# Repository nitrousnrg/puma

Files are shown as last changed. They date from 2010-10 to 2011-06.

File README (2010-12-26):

This is the hardware design of FreeEMS, a free engine management system.

Originally developed by jharvey, this branch uses his schematics, but adds a few extra circuits and redesigns the pcb, in order to fit the argentinian market better.

This design is NOT INTENDED to be as configurable as the official hardware, but to be suitable for production.

Main goals are:
* SMD
* 2 layers, 10x13cm board
* connector board for engine interface
* industrial grade specs
* 8 hi/low Z injector outputs
* 4 ignition outputs
* fuel pump control
* stepper motor control
* 2 aux power outputs
* MAP, AAP, MAF, TPS, lambda, battery voltage, EGT, MAT, IAT, CLT, aux temperature input, aux GP input
* 6 protected GPIO
* USB for tuning and datalogging

Planned release: 20/6/2011 (or never)

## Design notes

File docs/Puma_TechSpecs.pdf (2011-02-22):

Puma is an automotive-grade board designed to run FreeEMS vanilla code, an Open Source Engine Management System destined to liberate engines all around the globe. This piece of hardware was meant to meet the highest reliability standards, and to provide most of the functions needed by engine tuners. It has the potential to sequentially drive up to 8 cylinder engines, controlling both fuel and ignition (wasted spark), or dual rail 4 cylinders setups, 6cyl, etc. With the appropiate firmware, almost anything can be done.

These boards come with military temperature specs, and plenty of heavy duty components.

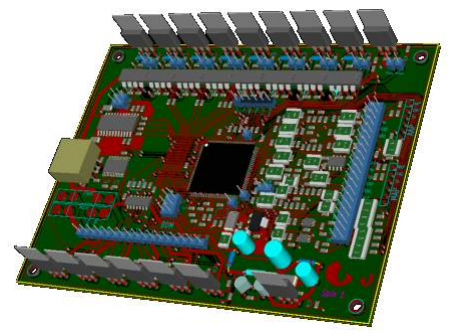
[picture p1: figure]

### Capabilities

Every board is equipped with the following items:

- USB connection for engine tuning, datalogging, and firmware updates.
- Compact SMD assembly.
- 8 outputs for low impedance injectors.
- 4 ignition outputs.
- 2 general purpose power outputs.
- 12 analog inputs
- 12 digital general purpose I/O
- Stepper driver
- Fuel pump relay control
- CAN and SPI communications
- Connector board to suit different setups, allow extra features, and provide different connectors or prototyping areas.

### Inputs

- MAP (Manifold Absolute Pressure)
- MAF (Mass Air Flow sensor)
- CHT (Coolant temperature)
- AAP (Atmospheric Absolute Pressure)
- IAT (Intake Air Temperature)
- EGO (Exhaust Gas Oxygen)
- BVR (Battery Voltage Reference)
- MAT (Manifold Air Temperature)
- EGT (Exhaust Gas Temperature)
- Aux NTC sensor
- General purpose analog input
- 2 VR inputs

### Outputs

- 8 Peak & Hold injector drivers supplying up to 4 Amps each.
- 4 ignition outputs, intended to drive external ignition modules, although ignition drivers can be installed.
- 2 PWM outputs, capable of delivering many amps to solenoid valves, switches, servos, etc.
- 1 output for controlling the fuel pump relay

Extra CPU pins can be used through specific connector boards (not designed yet!), for example

- 2 extra ignition outputs can be used for 6 cylinders COP setups
- Up to 10 general purpose power outputs (pumps, nitrous triggers, extra solenoids, etc)

### Specs

- Input voltage: 6.5v-32v (to be tested)
- Operating temperature: -40°C to 125°C (its the target, still not reached)
- Reverse battery protection
- All inputs protected from overvoltages.
- Power outputs clamped to 33v (can change soon)

### Connector board

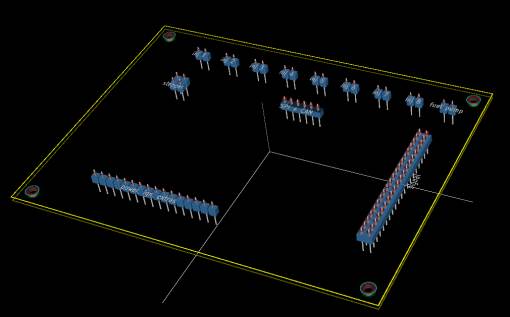
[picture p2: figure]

The first draft is still subject to change, until we find a better way to connect the high power parts.

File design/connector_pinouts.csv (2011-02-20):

connector pin outs (for spin 1 of puma)
P99
pin | MCU/destination | nick name | DIGI PROTECT | AN PROTECT | PG (1 AND …) | bried descrition
1 |  | MAT |  |  | 26 | MAS AIR TEMP THERMISTOR INPUT PG 26
2 |  | AGND |  |  | 26
3 |  | AUX IN |  |  | 10
4 |  | GP_NTC |  |  | 10 23 25 | THERMISTOR INPUT PG25
5 |  | AGND |  |  | 25 | THERMISTOR INPUT PG25
6 |  | 5 |  |  | 44
7 |  | MAP |  |  | 44 | NOT AAP
8 |  | AGND? |  |  | 44
9 |  | O2+ |  | Y | 49 | O2+
10 |  | O2GND |  |  | 49 | O2 AGND
11 |  |  |  |  |  | NC
12 |  |  |  |  |  | NC
13 |  |  |  |  |  | NC
14 |  |  |  |  |  | NC
15 |  | MAF |  |  | 23
16 | PM2 | DGP |  |  | 1 | Digital General Purpose include digi_protect sub circuit
17 |  | K+ |  |  | 21 | EGT +
18 | PM3 | DGP |  |  | 1 | Digital General Purpose include digi_protect sub circuit
19 |  | K- |  |  | 21 | EGT -
20 |  | 5 |  |  | 54 | TPS +5
21 |  | TPS |  |  | 54 | THROTTLE POSITION SENSOR
22 |  | AGND |  |  | 54 | TPS AGND
23 |  | CHT |  |  | 55 | THERMISTER INPUT
24 |  | AGND |  |  | 55
25 |  | IAT |  |  | 56 | INTAKE AIR TEMP THERMISTER INPUT
26 |  | AGND |  |  | 56
27 | PJ0 | DGP |  |  | 1 | Digital General Purpose include digi_protect sub circuit
28 | PJ1 | DGP |  |  | 1 | Digital General Purpose include digi_protect sub circuit
29 | PJ6 | DGP |  |  | 1 | Digital General Purpose include digi_protect sub circuit
30 | PJ7 | DGP |  |  | 1 | Digital General Purpose include digi_protect sub circuit
31 | PM0 | DGP |  |  | 1 | Digital General Purpose include digi_protect sub circuit
32 | PM1 | DGP |  |  | 1 | Digital General Purpose include digi_protect sub circuit
33 | PP6 | DGP |  |  | 1 | Digital General Purpose include digi_protect sub circuit
34 | PP7 | DGP |  |  | 1 | Digital General Purpose include digi_protect sub circuit
35 | PT6 | DGP |  |  | 1 | Digital General Purpose include digi_protect sub circuit
36 | PT7 | DGP |  |  | 1 | Digital General Purpose include digi_protect sub circuit
37 |  | VR1- |  |  | 18
38 |  | VR1+ |  |  | 18
39 |  | VR2- |  |  | 5
40 |  | VR2+ |  |  | 5
misc pins
p103 | PH0 |  |  |  | 1 | direct to MCU, not protection, placed where ever it fit/near MCU
p104 | PS3 |  |  |  | 1 | direct to MCU, not protection, placed where ever it fit/near MCU

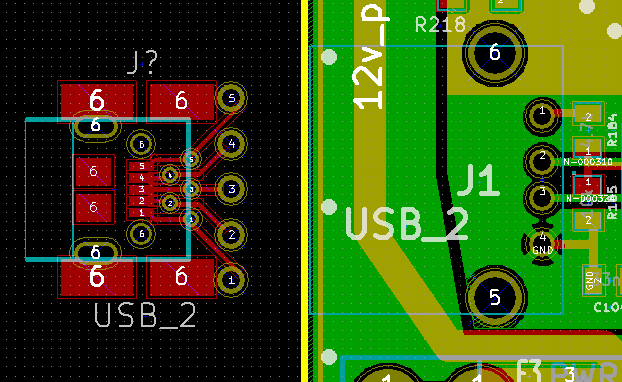
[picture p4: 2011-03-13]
PCB-modules/micro-mini-header.PNG

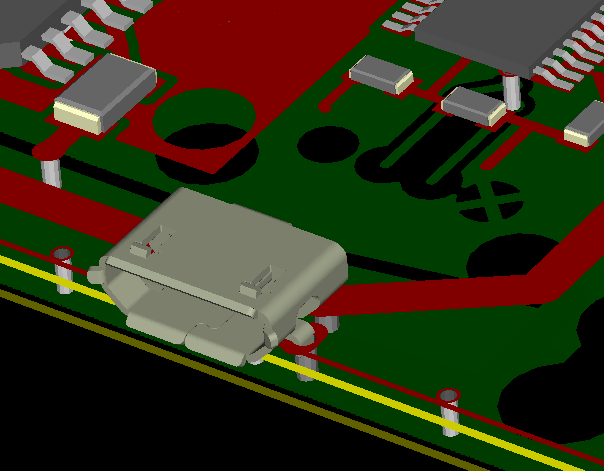
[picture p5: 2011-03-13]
PCB-modules/USB uB/USB_uB_snapshot.png

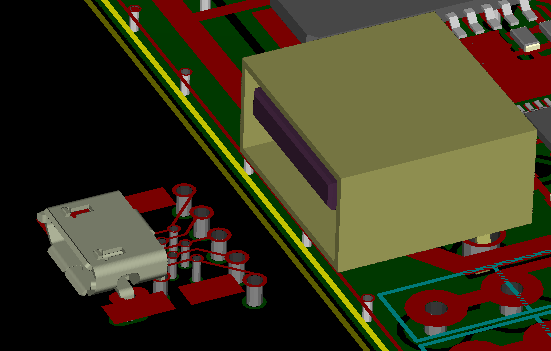
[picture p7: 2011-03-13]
PCB-modules/micro-mini-header-iso-u.PNG

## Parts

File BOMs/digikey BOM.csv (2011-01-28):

Digi-Key Part Number | Description | Mouser number | Optional? | Quantity 1 | Quantity 2
490-1664-1-ND | .01uF |  |  | 9
490-1666-2-ND | .1uF |  |  | 25
WHCR10FECT-ND | 0.1 2W |  | P&H | 8
490-1666-2-ND | 0.1uF |  |  | 15
311-1128-1-ND | 1.5nF |  |  | 11
RMCF0805JT1K00CT-ND | 1.6k |  |  | 9
RMCF0805JT100KCT-ND | 100k |  |  | 3
WK6242-ND | 10A |  |  | 1
RMCF0805JT10K0CT-ND | 10k |  |  | 25
RMCF0805JT10M0CT-ND | 10M |  |  | 1
311-1099-1-ND | 10pF |  |  | 3
493-1279-ND | 10uF |  |  | 2
644-1129-1-ND | 16MHZ |  |  | 1
RMCF0805JT1K00CT-ND | 1K |  |  | 64
1N4007DICT-ND | 1N4007 |  |  | 1
1N4148WTPMSCT-ND | 1N4148 |  |  | 14
1N4448W-FDICT-ND | 1N4448 |  |  | 1
1.0W-2-ND | 1R |  |  | 1
541-1.0VCT-ND | 1R 1W |  | Stepper driver | 2
RMCF0805JT2K20CT-ND | 2.2k |  |  | 7
565-1634-ND | 2200uF |  |  | 1
RMCF0805JT22K0CT-ND | 22k |  |  | 3
709-1172-1-ND | 22pF |  |  | 2
478-3901-1-ND | 22uF |  |  | 2
RMCF0805JT270RCT-ND | 270R |  |  | 2
620-1158-1-ND | 2916 |  | Stepper driver | 1
WK6242-ND | 2A |  | Fuse | 1
2N6045GOS-ND | 2N6044 |  | P&H | 8
RMCF0805JT3K30CT-ND | 3.3k |  |  | 16
399-1151-1-ND | 3.3nF |  |  | 1
RMCF0805JT1K00CT-ND | 3.9K |  |  | 1
311-1123-1-ND | 330pF |  |  | 1
478-3550-1-ND | 33nF |  |  | 9
1N5364BRLGOSCT-ND | 33v 5w |  | P&H | 8
RMCF0805JT39K0CT-ND | 39k |  |  | 13
RMCF0805JT4K70CT-ND | 4.7k |  |  | 2
BZT52C5V1-FDICT-ND | 5.1v |  |  | 12
BZT52C5V1-FDICT-ND | 5V1 |  |  | 6
P680KACT-ND | 680k |  |  | 3
RMCF0805JT68K0CT-ND | 68k |  |  | 1
74HC86DR2GOSCT-ND | 74LS86 |  | XOR gate for ignition | 1
AD8497ARMZ-ND | AD597 |  | EGT driver | 1
1N4148WTPMSCT-ND | DIODE |  |  | 4
768-1007-1-ND | FT232RL |  |  | 1
475-1415-1-ND | LED |  |  | 18
LM1949N-ND | LM1949 |  | P&H | 8
LM2937ET-5.0-ND | LM2937 |  |  | 1
MAX9924UAUB+-ND | MAX9924 |  |  | 2
MC9S12XDP512MAL-ND | MC9S12XDP512 |  |  | 1
LM2937IMP-5.0CT-ND | LM2937-SOT223 |  |  | 1
MPX4100A-ND | MPX4100A |  | AAP sensor | 1
MPX4250AP-ND | MPX4250A |  | MAP sensor | 1
RFP30N06LE-ND | RFP30N06 |  | monster mosfet | 6
RFP30N06LE-ND | RFP30N06LE |  | monster mosfet | 1
MBR0520LCT-ND | SCHOTTKY |  |  | 12
UE27AC54100-ND | USB_2 |  |  | 1
AE1454-ND | USB male A-male A cable |  | connector could be changed | 1

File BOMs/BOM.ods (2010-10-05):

Description | Digikey number | Mouser number | Quantity | $ | Parts
CPU | MC9S12XDP512MAL-ND | 841-MC9S12XDP512MAG | 2 | 23.52 | 47.04
6ch digital isolator | -- | 634-SI8460AA-B-IS1 | 2 | 2.86 | 5.72
P&H driver | LM1949N-ND | -- | 8 | 4.87 | 38.96
2N6044 | -- | 610-2N6044 | 8 | 1.15 | 9.2
0.1uF cap | 490-1666-2-ND |  | 3,000 | 0.007 | 21
10pF cap | 311-1099-1-ND |  | 100 | 0.02980 | 2.98
0.1ohm 2W | WHCR10FECT-ND |  | 8 | 0.93 | 7.44
1ohm |  |  |  |  | 0
270ohm | RMCF0603JT270RCT-ND |  | 100 | 0.007 | 0.7
1k | RMCF0603JT1K00CT-ND |  | 100 | 0.007 | 0.7
2.2k | RMCF0603JT2K20CT-ND |  | 100 | 0.007 | 0.7
3.3k | RMCF0603JT3K30CT-ND |  | 100 | 0.007 | 0.7
4.7k | RMCF0603JT4K70CT-ND |  | 100 | 0.007 | 0.7
5.6k | RMCF0603JT5K60CT-ND |  | 100 | 0.007 | 0.7
10k | RMCF0603JT10K0CT-ND |  | 100 | 0.007 | 0.7
13k | -- |  |  |  | 0
18k | -- |  |  |  | 0
22k | RMCF0603JT22K0CT-ND |  | 100 | 0.007 | 0.7
39k | P39KGCT-ND |  | 100 | 0.00790 | 0.79
68k | RMCF0603JT68K0CT-ND |  | 100 | 0.007 | 0.7
100k | RMCF0603JT100KCT-ND |  | 100 | 0.007 | 0.7
680k | P680KGCT-ND |  | 100 | 0.0079 | 0.79
1.6M | P1.6MGCT-ND |  | 100 | 0.0079 | 0.79
10M | RMCF0603JT10M0CT-ND |  | 100 | 0.007 | 0.7
LM1815 | LM1815M-ND | -- | 4 |  | 0
MAX9924 | MAX9924UAUB+-ND |  | 2 | 2.52 | 5.04
5v digital reg | LM2940T-5.0-ND |  | 3 | 1.77 | 5.31
5v analog reg | LM2936MX-5.0CT-ND |  | 2 | 2.38 | 4.76
ad596 | -- | -- |  |  | 0
FT232RL | 768-1007-1-ND |  | 2 | 4.5 | 9
16MHz crystal | 535-9948-1-ND |  | 2 | 1.01 | 2.02
fuse holder | WK6242-ND |  | 10 | 0.135 | 1.35
sckottky diode | MBR0520LCT-ND |  | 100 | 0.1936 | 19.36
5.1v zener | BZT52C5V1-FDICT-ND |  | 30 | 0.25500 | 7.65
0805 green LED | 160-1179-1-ND |  | 100 | 0.05800 | 5.8
1N4148 | 1N4148WTPMSCT-ND |  | 30 | 0.25500 | 7.65
 |  |  |  |  | 210.35

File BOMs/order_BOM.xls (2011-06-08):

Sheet: FreeEMS_setup
description | qty | notes | component | bare min |  | recommended |  | INJ-H |  | INJ-L |  | IGN |  | RPM |  | MAPB |  | MAPN |  | AAP |  | MAF |  | GPO |  | O2 |  | EGT |  | TCPL |  | AN |  | STP |  | ANP |  | DGP |  | Total
bare min parts | 1 | required (MCU, PLL, TPS, USB, BDM, 5V reg, ect) | description | qty/ea |  | qty/ea |  | qty/ea |  | qty/ea |  | qty/ea |  | qty/ea |  | qty/ea |  | qty/ea |  | qty/ea |  | qty/ea |  | qty/ea |  | qty/ea |  | qty/ea |  | qty/ea |  | qty/ea |  | qty/ea |  | qty/ea |  | qty/ea |  |  | NOTES
recommended | 1 | (SWVreg, XOR, stepper) | 2916 (stepper) |  | 0 | 1 | 1 |  | 0 |  | 0 |  | 0 |  | 0 |  | 0 |  | 0 |  | 0 |  | 0 |  | 0 |  | 0 |  | 0 |  | 0 |  | 0 |  | 0 |  | 0 |  | 0 | 1
 |  |  | 1K | 1 | 1 | 4 | 4 |  | 0 |  | 0 | 1 | 1 |  | 0 |  | 0 |  | 0 |  | 0 |  | 0 |  | 0 |  | 0 |  | 0 |  | 0 |  | 0 |  | 0 | 2 | 2 |  | 0 | 8
 |  | Outputs | 1R | 1 | 1 | 2 | 2 |  | 0 |  | 0 |  | 0 |  | 0 |  | 0 |  | 0 |  | 0 |  | 0 |  | 0 |  | 0 |  | 0 |  | 0 |  | 0 |  | 0 |  | 0 |  | 0 | 3
INJ-H | 1 | [max 8] Fuel highZ (8 max low and high) | 2A | 1 | 1 |  | 0 |  | 0 |  | 0 |  | 0 |  | 0 |  | 0 |  | 0 |  | 0 |  | 0 |  | 0 |  | 0 |  | 0 |  | 0 |  | 0 |  | 0 |  | 0 |  | 0 | 1
INJ-L | 1 | [max 8] Fuel lowZ (8 max low and high) | 10k | 11 | 11 |  | 0 |  | 0 |  | 0 | 1 | 1 | 3 | 6 |  | 0 |  | 0 |  | 0 | 1 | 1 |  | 0 |  | 0 |  | 0 |  | 0 |  | 0 |  | 0 |  | 0 |  | 0 | 19
IGN | 1 | [max 4] Ignition (external drivers) | 10M | 2 | 2 |  | 0 |  | 0 |  | 0 |  | 0 |  | 0 |  | 0 |  | 0 |  | 0 |  | 0 |  | 0 |  | 0 |  | 0 |  | 0 |  | 0 |  | 0 |  | 0 |  | 0 | 2
 |  |  | 22k | 1 | 1 |  | 0 |  | 0 |  | 0 |  | 0 |  | 0 |  | 0 |  | 0 |  | 0 |  | 0 |  | 0 |  | 0 |  | 0 |  | 0 |  | 0 |  | 0 |  | 0 |  | 0 | 1
 |  | Sensors | 39k | 1 | 1 |  | 0 |  | 0 |  | 0 |  | 0 |  | 0 |  | 0 |  | 0 |  | 0 |  | 0 |  | 0 |  | 0 |  | 0 |  | 0 |  | 0 |  | 0 |  | 0 |  | 0 | 1
RPM | 2 | [max 2] good for 0-5V hall input(s) and VR input(s) | 5V1zener |  | 0 |  | 0 |  | 0 |  | 0 |  | 0 |  | 0 |  | 0 |  | 0 |  | 0 |  | 0 |  | 0 |  | 0 |  | 0 |  | 0 |  | 0 |  | 0 |  | 0 | 1 | 1 | 1
MAPB | 1 | [max 1] boosted (1 MAP only) | 68k |  | 0 |  | 0 |  | 0 |  | 0 |  | 0 |  | 0 | 1 | 1 | 1 | 1 |  | 0 |  | 0 |  | 0 |  | 0 |  | 0 |  | 0 |  | 0 |  | 0 |  | 0 |  | 0 | 2
MAPN | 1 | [max 1] Natural aspirated (1 MAP only) | .1uF(100nF) | 12 | 12 | 4 | 4 |  | 0 |  | 0 |  | 0 | 1 | 2 | 1 | 1 | 1 | 1 | 1 | 1 |  | 0 |  | 0 |  | 0 | 1 | 1 |  | 0 |  | 0 |  | 0 | 1 | 1 |  | 0 | 23
AAP | 1 | [max 1] Ambient Air Pressure | 1.6k | 9 | 9 | 4 | 4 |  | 0 | 1 | 1 | 1 | 1 |  | 0 |  | 0 |  | 0 |  | 0 |  | 0 | 1 | 1 |  | 0 |  | 0 |  | 0 |  | 0 |  | 0 |  | 0 | 1 | 1 | 17
MAF | 1 | [max 1] MAF VS MAP? | 100k |  | 0 |  | 0 |  | 0 |  | 0 |  | 0 |  | 0 |  | 0 |  | 0 |  | 0 |  | 0 | 1 | 1 |  | 0 |  | 0 |  | 0 |  | 0 |  | 0 |  | 0 |  | 0 | 1
GPO | 1 | [max 2] General Purpose Output | 10pF |  | 0 |  | 0 |  | 0 |  | 0 |  | 0 |  | 0 |  | 0 |  | 0 |  | 0 |  | 0 | 1 | 1 |  | 0 |  | 0 |  | 0 |  | 0 |  | 0 |  | 0 |  | 0 | 1
O2 | 1 | [max 2] Narrow band O2 | 10uF | 2 | 2 |  | 0 |  | 0 |  | 0 |  | 0 |  | 0 |  | 0 |  | 0 |  | 0 |  | 0 |  | 0 |  | 0 |  | 0 |  | 0 |  | 0 |  | 0 |  | 0 |  | 0 | 2
EGT | 1 | [max 1] Thermocouple (exhaust) | 2.2k |  | 0 |  | 0 |  | 0 |  | 0 |  | 0 |  | 0 |  | 0 |  | 0 |  | 0 |  | 0 |  | 0 |  | 0 |  | 0 | 1 | 4 |  | 0 |  | 0 |  | 0 |  | 0 | 4 | SNUBBER DIODE FOOTPRINT PLACE HOLDER
TCPL | 4 | [max 4] Hermiston (IAT, CHT, MAT, MISC) | 22pF | 2 | 2 |  | 0 |  | 0 |  | 0 |  | 0 |  | 0 |  | 0 |  | 0 |  | 0 |  | 0 |  | 0 |  | 0 |  | 0 |  | 0 |  | 0 |  | 0 |  | 0 |  | 0 | 2
AN | 1 | [max 1] misc analog | 22uF | 2 | 2 |  | 0 |  | 0 |  | 0 |  | 0 |  | 0 |  | 0 |  | 0 |  | 0 |  | 0 |  | 0 |  | 0 |  | 0 |  | 0 |  | 0 |  | 0 |  | 0 |  | 0 | 2
STP | 1 | [max 1] stepper driver | 270R | 2 | 2 |  | 0 |  | 0 |  | 0 |  | 0 |  | 0 |  | 0 |  | 0 |  | 0 |  | 0 |  | 0 |  | 0 |  | 0 |  | 0 |  | 0 |  | 0 |  | 0 |  | 0 | 2
ANP | 1 | [max 16] analog protect | 3.3k |  | 0 |  | 0 |  | 0 |  | 0 |  | 0 |  | 0 |  | 0 |  | 0 |  | 0 |  | 0 |  | 0 |  | 0 |  | 0 |  | 0 |  | 0 |  | 0 |  | 0 |  | 0 | 0 | REPLACED BY ? Not found in KICAD
DGP | 1 | [max 12] digi protect | 3.9K | 2 | 2 |  | 0 |  | 0 | 1 | 1 |  | 0 |  | 0 |  | 0 |  | 0 |  | 0 |  | 0 |  | 0 |  | 0 |  | 0 |  | 0 |  | 0 |  | 0 |  | 0 |  | 0 | 3
 |  |  | 33nF | 4 | 4 |  | 0 |  | 0 |  | 0 |  | 0 |  | 0 | 1 | 1 | 1 | 1 |  | 0 |  | 0 |  | 0 |  | 0 |  | 0 |  | 0 |  | 0 |  | 0 |  | 0 |  | 0 | 6
 |  |  | 4.7k | 2 | 2 |  | 0 |  | 0 |  | 0 |  | 0 |  | 0 |  | 0 |  | 0 |  | 0 |  | 0 |  | 0 |  | 0 |  | 0 |  | 0 |  | 0 |  | 0 |  | 0 |  | 0 | 2
 |  | Enter data on green cells | 680k |  | 0 |  | 0 |  | 0 |  | 0 |  | 0 |  | 0 | 1 | 1 | 1 | 1 |  | 0 | 1 | 1 |  | 0 |  | 0 |  | 0 |  | 0 |  | 0 |  | 0 |  | 0 |  | 0 | 3
 |  | See notes on recommended max qty's for each | .01uF (10nF) |  | 0 |  | 0 |  | 0 | 1 | 1 |  | 0 | 1 | 2 |  | 0 |  | 0 | 1 | 1 |  | 0 |  | 0 |  | 0 |  | 0 |  | 0 |  | 0 |  | 0 |  | 0 |  | 0 | 4
 |  | sub circuit. This will generate the BOM to be ordered. | 0805LED | 2 | 2 |  | 0 |  | 0 |  | 0 | 1 | 1 |  | 0 |  | 0 |  | 0 |  | 0 |  | 0 |  | 0 |  | 0 |  | 0 |  | 0 |  | 0 |  | 0 |  | 0 |  | 0 | 3
 |  | After the parts have been ordered and received, | 1.5nF | 8 | 8 |  | 0 |  | 0 |  | 0 |  | 0 |  | 0 | 1 | 1 | 1 | 1 |  | 0 |  | 0 |  | 0 |  | 0 |  | 0 |  | 0 |  | 0 |  | 0 |  | 0 |  | 0 | 10
 |  | use a different BOM to place the components, via | 16MHZ | 1 | 1 |  | 0 |  | 0 |  | 0 |  | 0 |  | 0 |  | 0 |  | 0 |  | 0 |  | 0 |  | 0 |  | 0 |  | 0 |  | 0 |  | 0 |  | 0 |  | 0 |  | 0 | 1
 |  | ref designators. | 1N4148diode |  | 0 |  | 0 |  | 0 |  | 0 |  | 0 |  | 0 |  | 0 |  | 0 |  | 0 |  | 0 |  | 0 |  | 0 |  | 0 |  | 0 |  | 0 |  | 0 |  | 0 | 1 | 1 | 1
 |  |  | 1R1W |  | 0 |  | 0 |  | 0 |  | 0 |  | 0 |  | 0 |  | 0 |  | 0 |  | 0 |  | 0 |  | 0 |  | 0 |  | 0 |  | 0 |  | 0 | 2 | 2 |  | 0 |  | 0 | 2 | 1R LINE E5?
 |  | Cell protection password is blank, protection prevents | 3.3nF | 1 | 1 |  | 0 |  | 0 |  | 0 |  | 0 |  | 0 |  | 0 |  | 0 |  | 0 |  | 0 |  | 0 |  | 0 |  | 0 |  | 0 |  | 0 |  | 0 |  | 0 |  | 0 | 1
 |  | accidental error edits. | 330pF | 1 | 1 |  | 0 |  | 0 |  | 0 |  | 0 |  | 0 |  | 0 |  | 0 |  | 0 |  | 0 |  | 0 |  | 0 |  | 0 |  | 0 |  | 0 |  | 0 |  | 0 |  | 0 | 1
 |  |  | AD597 |  | 0 |  | 0 |  | 0 |  | 0 |  | 0 |  | 0 |  | 0 |  | 0 |  | 0 |  | 0 |  | 0 |  | 0 | 1 | 1 |  | 0 |  | 0 |  | 0 |  | 0 |  | 0 | 1
 |  | rev A Spin 1 Draft | USB_2 | 1 | 1 |  | 0 |  | 0 |  | 0 |  | 0 |  | 0 |  | 0 |  | 0 |  | 0 |  | 0 |  | 0 |  | 0 |  | 0 |  | 0 |  | 0 |  | 0 |  | 0 |  | 0 | 1
 |  |  | 0.1R2W |  | 0 |  | 0 |  | 0 | 1 | 1 |  | 0 |  | 0 |  | 0 |  | 0 |  | 0 |  | 0 |  | 0 |  | 0 |  | 0 |  | 0 |  | 0 |  | 0 |  | 0 |  | 0 | 1
 |  | Items of question | 1N4007 | 3 | 3 |  | 0 |  | 0 |  | 0 |  | 0 |  | 0 |  | 0 |  | 0 |  | 0 |  | 0 |  | 0 |  | 0 |  | 0 |  | 0 |  | 0 |  | 0 |  | 0 |  | 0 | 3
 |  | C95 | 1N4148 | 1 | 1 |  | 0 |  | 0 |  | 0 |  | 0 |  | 0 |  | 0 |  | 0 |  | 0 |  | 0 |  | 0 |  | 0 |  | 0 |  | 0 |  | 0 |  | 0 | 1 | 1 |  | 0 | 2
 |  | mic2954 | 1N4448 |  | 0 |  | 0 |  | 0 |  | 0 |  | 0 |  | 0 |  | 0 |  | 0 |  | 0 |  | 0 |  | 0 |  | 0 |  | 0 |  | 0 |  | 0 |  | 0 |  | 0 |  | 0 | 0 | ???
 |  | low side drive mosfets | 2200uF | 1 | 1 |  | 0 |  | 0 |  | 0 |  | 0 |  | 0 |  | 0 |  | 0 |  | 0 |  | 0 |  | 0 |  | 0 |  | 0 |  | 0 |  | 0 |  | 0 |  | 0 |  | 0 | 1
 |  | R151 | 2N6045 |  | 0 |  | 0 |  | 0 | 1 | 1 |  | 0 |  | 0 |  | 0 |  | 0 |  | 0 |  | 0 |  | 0 |  | 0 |  | 0 |  | 0 |  | 0 |  | 0 |  | 0 |  | 0 | 1
 |  | R150 | 33v5w |  | 0 |  | 0 |  | 0 | 1 | 1 |  | 0 |  | 0 |  | 0 |  | 0 |  | 0 |  | 0 |  | 0 |  | 0 |  | 0 |  | 0 |  | 0 |  | 0 |  | 0 |  | 0 | 1
 |  | SEE ROW 59 AND COLUM AR??? | 74HC86 |  | 0 | 1 | 1 |  | 0 |  | 0 |  | 0 |  | 0 |  | 0 |  | 0 |  | 0 |  | 0 |  | 0 |  | 0 |  | 0 |  | 0 |  | 0 |  | 0 |  | 0 |  | 0 | 1
 |  |  | LM1949 |  | 0 |  | 0 |  | 0 | 1 | 1 |  | 0 |  | 0 |  | 0 |  | 0 |  | 0 |  | 0 |  | 0 |  | 0 |  | 0 |  | 0 |  | 0 |  | 0 |  | 0 |  | 0 | 1
 |  |  | LM2940 | 2 | 2 |  | 0 |  | 0 |  | 0 |  | 0 |  | 0 |  | 0 |  | 0 |  | 0 |  | 0 |  | 0 |  | 0 |  | 0 |  | 0 |  | 0 |  | 0 |  | 0 |  | 0 | 2
 |  |  | FT232RL | 1 | 1 |  | 0 |  | 0 |  | 0 |  | 0 |  | 0 |  | 0 |  | 0 |  | 0 |  | 0 |  | 0 |  | 0 |  | 0 |  | 0 |  | 0 |  | 0 |  | 0 |  | 0 | 1
 |  |  | MAX9924 |  | 0 |  | 0 |  | 0 |  | 0 |  | 0 | 1 | 2 |  | 0 |  | 0 |  | 0 |  | 0 |  | 0 |  | 0 |  | 0 |  | 0 |  | 0 |  | 0 |  | 0 |  | 0 | 2
 |  |  | LM2937-SOT223 | 1 | 1 |  | 0 |  | 0 |  | 0 |  | 0 |  | 0 |  | 0 |  | 0 |  | 0 |  | 0 |  | 0 |  | 0 |  | 0 |  | 0 |  | 0 |  | 0 |  | 0 |  | 0 | 1
 |  |  | MPX4100A |  | 0 |  | 0 |  | 0 |  | 0 |  | 0 |  | 0 |  | 0 |  | 0 | 1 | 1 |  | 0 |  | 0 |  | 0 |  | 0 |  | 0 |  | 0 |  | 0 |  | 0 |  | 0 | 1
 |  |  | MPX4100AP |  | 0 |  | 0 |  | 0 |  | 0 |  | 0 |  | 0 | 0 | 0 | 1 | 1 |  | 0 |  | 0 |  | 0 |  | 0 |  | 0 |  | 0 |  | 0 |  | 0 |  | 0 |  | 0 | 1
 |  |  | MPX4250AP |  | 0 |  | 0 |  | 0 |  | 0 |  | 0 |  | 0 | 1 | 1 |  | 0 |  | 0 |  | 0 |  | 0 |  | 0 |  | 0 |  | 0 |  | 0 |  | 0 |  | 0 |  | 0 | 1
 |  |  | VNP20N07 |  | 0 |  | 0 | 1 | 1 |  | 0 | 1 | 1 |  | 0 |  | 0 |  | 0 |  | 0 |  | 0 | 1 | 1 |  | 0 |  | 0 |  | 0 |  | 0 |  | 0 |  | 0 |  | 0 | 2
 |  |  | SCHOTTKY |  | 0 |  | 0 |  | 0 |  | 0 |  | 0 |  | 0 |  | 0 |  | 0 |  | 0 |  | 0 |  | 0 |  | 0 |  | 0 |  | 0 |  | 0 |  | 0 | 1 | 1 |  | 0 | 1
 |  |  | MC9S12XDP512 | 1 | 1 |  | 0 |  | 0 |  | 0 |  | 0 |  | 0 |  | 0 |  | 0 |  | 0 |  | 0 |  | 0 |  | 0 |  | 0 |  | 0 |  | 0 |  | 0 |  | 0 |  | 0 | 1
 |  |  | USB maleA-maleA cable | 1 | 1 |  | 0 |  | 0 |  | 0 |  | 0 |  | 0 |  | 0 |  | 0 |  | 0 |  | 0 |  | 0 |  | 0 |  | 0 |  | 0 |  | 0 |  | 0 |  | 0 |  | 0 | 1
 |  |  |  |  |  |  |  |  |  | C123?? |  |  |  |  |  |  |  |  |  | C21??

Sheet: MFG BOM
Mouser number | Newark Part number | Digi-Key Part Number | MFG | MFG# | Description | Notes | QTYfromsheet"FreeEMS_setup" | Quantity1 | Comments
 |  | 620-1158-1-ND | Allegro Microsystems Inc | UDQ2916LBTR-T | 2916 (stepper) | Stepperdriver | 1 | 1 | Never been tested,and there is no code to support iit yet.
 |  | RHM1.00KCRCT-ND |  | MCR10EZPF1001 | 1K |  | 8 | 64 | 1%
 |  | 1.0W-2-ND |  | RSF200JB-1R0 | 1R |  | 3 | 1
 |  | WK6242-ND |  | 52000001009 | 2A | Fuse | 1 | 1 | Fuses should be outside the board, wwith all the other fuses of the car.
 |  | RMCF0805FT10K0TR-ND |  | RMCF0805FT10K0 | 10k |  | 19 | 25 | 1%
 |  | RMCF0805JT10M0CT-ND |  | RMCF0805JT10M0 | 10M |  | 2 | 1
 |  | RMCF0805JT22K0CT-ND |  | RMCF0805JT22K0 | 22k |  | 1 | 3
 |  | RHM39.0KCRCT-ND |  | MCR10EZPF3902 | 39k |  | 1 | 13 | 1%
 |  | BZT52C5V1-FDICT-ND |  | BZT52C5V1-7-F | 5V1zener |  | 1 | 6
 |  | RMCF0805JT68K0CT-ND |  | RMCF0805JT68K0 | 68k |  | 2 | 1
 |  | 490-1666-2-ND |  | GRM21BR71H104KA01L | .1uF(100nF) |  | 23 | 25
 |  | RMCF0805JT1K60CT-ND |  | RMCF0805JT1K60 | 1.6k |  | 17 | 9
 |  | RMCF0805JT100KCT-ND |  | RMCF0805JT100K | 100k |  | 1 | 3
 |  | 311-1099-1-ND |  | CC0805JRNP09BN100 | 10pF |  | 1 | 3
 |  | 493-1279-ND |  | UVZ1C100MDD | 10uF |  | 2 | 2 | If you don't like electrolitics, don' tbuy it
 |  | RHM2.20KCRCT-ND |  | MCR10EZPF2201 | 2.2k |  | 4 | 7 | 1%
 |  | 709-1172-1-ND |  | 500R15N220JV4T | 22pF |  | 2 | 2
 |  | 478-3901-1-ND |  | TAJC226M016RNJ | 22uF |  | 2 | 2
 |  | RMCF0805JT270RCT-ND |  | RMCF0805JT270R | 270R |  | 2 | 2
 |  | RHM3.30KCRCT-ND |  | MCR10EZPF3301 | 3.3k |  | 0 | 16 | 1%
 |  | RHM3.90KCRCT-ND |  | MCR10EZPF3901 | 3.9K |  | 3 | 1 | 1%
 |  | 478-3550-1-ND |  | 08055C333KAZ2A | 33nF |  | 6 | 9
 |  | RMCF0805JT4K70CT-ND |  | RMCF0805JT4K70 | 4.7k |  | 2 | 2
 |  | P680KACT-ND |  | ERJ-6GEYJ684V | 680k |  | 3 | 3
 |  | 490-1664-1-ND |  | GRM216R71H103KA01D | .01uF (10nF) |  | 4 | 9
 |  | 475-1415-1-ND |  | LH R974-LP-1-0-20-R18 | 0805LED |  | 3 | 18 | Its just aled! Choose other colors if you want.
 |  | 311-1128-1-ND |  | CC0805KRX7R9BB152 | 1.5nF |  | 10 | 11
 |  | 644-1129-1-ND |  | NX3225SA 16MHZ AT-W | 16MHZ |  | 1 | 1
 |  | 1N4148WTPMSCT-ND | Micro Commercial Co | 1N4148W-TP | 1N4148diode |  | 1 | 4
 |  | 541-1.0VCT-ND |  | CRCW12101R00JNEA | 1R1W | Stepperdriver | 2 | 2 | Neverbeentested,andthereisnocodetosupportiityet.
 |  | 709-1192-1-ND |  | 500R15W332KV4T | 3.3nF |  | 1 | 1
 |  | 311-1192-1-ND |  | CC0805KRX7R9BB331 | 330pF |  | 1 | 1
 |  | AD8497ARMZ-ND | Analog Devices Inc | AD8497ARMZ | AD597 | EGTdriver | 1 | 1 | itwon'tmeasuremorethan500Â°C!
 |  | UE27AC54100-ND | Amphenol Commercial Products | UE27AC54100 | USB_2 |  | 1 | 1 | Thisconnectorfitstheboard,butitsquiteprobableyouwon'thaveacableforit.
 |  | WHCR10FECT-ND | Ohmite | WHCR10FET | 0.1R2W | P&H | 1 | 8
 |  | 1N4007DICT-ND | Diodes Inc | 1N4007-T | 1N4007 |  | 3 | 1
 |  | 1N4148WTPMSCT-ND | Micro Commercial Co | 1N4148W-TP | 1N4148 |  | 2 | 14
 |  | 1N4448W-FDICT-ND | Diodes Inc | 1N4448W-7-F | 1N4448 |  | 0 | 1
 |  | 565-1634-ND | United Chemi-Con | EKZE6R3ELL222MJ25S | 2200uF |  | 1 | 1 | Toobig,toounreliable.I'mnotinstallingit(marcos)
 |  | 2N6045GOS-ND | On Semiconductor | 2N6045G | 2N6045 | P&H | 1 | 8 | Transistorsthatdrivestheinjectors.Ifyoudon'tuselow-z,youshouldbuyautofets.
 |  | 1N5364BRLGOSCT-ND | ON Semiconductor | 1N5364BRLG | 33v5w | P&H | 1 | 8 | Itsinsanelyhuge!
 |  | 74HC86DR2GOSCT-ND | ON Semiconductor | 74HC86DR2G | 74HC86 | XOR gate for ignition | 1 | 1 | Tip:itcandriveanignmoduledirectly,withoutextraFETs
 |  | LM1949N-ND | National Semiconductor | LM1949N/NOPB | LM1949 | P&H | 1 | 8
 |  | LM2940T-5.0-ND | National Semiconductor | LM2940T-5.0/NOPB | LM2940 |  | 2 | 1 | Mightwantsomethingtoscrewtoandisolatefromtheheatsink?
 |  | 768-1007-1-ND | FTDI | FT232RL-REEL | FT232RL |  | 1 | 1
 |  | MAX9924UAUB+-ND | Maxim Integrated Products | MAX9924UAUB+ | MAX9924 |  | 2 | 2 | Thisoneistiny,takeadeepbreathwhenyoudecidetosolderit.
 |  | LM2937IMP-5.0CT-ND | National Semiconductor | LM2937IMP-5.0/NOPB | LM2937-SOT223 |  | 1 | 1
 |  | MPX4100A-ND | Freescale Semiconductor | MPX4100A | MPX4100A | AAPsensor | 1 | 1
 |  | MPX4100AP-ND | Freescale Semiconductor | MPX4100AP | MPX4100AP | MAPsensor (NA)
 |  | MPX4250AP-ND | Freescale Semiconductor | MPX4250AP | MPX4250AP | MAPsensor (Boost) | 1 | 1
 |  | 497-2793-5-ND | STMicroelectronics | VNP20N07 | VNP20N07 | monstermosfet | 2 | 7 | thisisVERYbig...
 |  | MBR0520LCT-ND | Fairchild Semiconductor | MBR0520L | SCHOTTKY |  | 1 | 12 | thisisanicediode
 |  | MC9S12XDP512MAL-ND | Freescale Semiconductor | MC9S12XDP512MAL | MC9S12XDP512 |  | 1 | 1 | Checkiffreescalecansendyouafreesample
 |  | AE1454-ND | Assmann Electronics Inc | AK670/2-1-R | USB maleA-maleA cable | connector could be changed | 1 | 1 | Withthiscableyoucanusethestockconnector

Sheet: DIGIKEY BOM
Digi-Key Part No. | Manufacturer Name | Mfr Part No. | Customer Reference | Qty1 | Qty2 | Qty3
0 | 0 | 0 | 0 | 1
0 | 0 | 0 | 0 | 8
0 | 0 | 0 | 0 | 3
0 | 0 | 52000001009 | 0 | 1
0 | 0 | 0 | 0 | 19
0 | 0 | 0 | 0 | 2
0 | 0 | 0 | 0 | 1
0 | 0 | 0 | 0 | 1
0 | 0 | 0 | 0 | 1
0 | 0 | 0 | 0 | 2
0 | 0 | 0 | 0 | 23
0 | 0 | 0 | 0 | 17
0 | 0 | 0 | 0 | 1
0 | 0 | 0 | 0 | 1
0 | 0 | 0 | 0 | 2
0 | 0 | 0 | 0 | 4
0 | 0 | 0 | 0 | 2
0 | 0 | 0 | 0 | 2
0 | 0 | 0 | 0 | 2
0 | 0 | 0 | 0 | 0
0 | 0 | 0 | 0 | 3
0 | 0 | 0 | 0 | 6
0 | 0 | 0 | 0 | 2
0 | 0 | 0 | 0 | 3
0 | 0 | 0 | 0 | 4
0 | 0 | 0 | 0 | 3
0 | 0 | 0 | 0 | 10
0 | 0 | 0 | 0 | 1
0 | 0 | 0 | 0 | 1
0 | 0 | 0 | 0 | 2
0 | 0 | 0 | 0 | 1
0 | 0 | 0 | 0 | 1
0 | 0 | 0 | 0 | 1
0 | 0 | 0 | 0 | 1
0 | 0 | 0 | 0 | 1
0 | 0 | 0 | 0 | 3
0 | 0 | 0 | 0 | 2
0 | 0 | 0 | 0 | 0
0 | 0 | 0 | 0 | 1
0 | 0 | 0 | 0 | 1
0 | 0 | 0 | 0 | 1
0 | 0 | 0 | 0 | 1
0 | 0 | 0 | 0 | 1
0 | 0 | 0 | 0 | 2
0 | 0 | 0 | 0 | 1
0 | 0 | 0 | 0 | 2
0 | 0 | 0 | 0 | 1
0 | 0 | 0 | 0 | 1
0 | 0 | 0 | 0 | 0
0 | 0 | 0 | 0 | 1
0 | 0 | 0 | 0 | 2
0 | 0 | 0 | 0 | 1
0 | 0 | 0 | 0 | 1
0 | 0 | 0 | 0 | 1
0 | 0 | 0 | 0 | 0
0 | 0 | 0 | 0 | 0
0 | 0 | 0 | 0 | 0
0 | 0 | 0 | 0 | 0
0 | 0 | 0 | 0 | 0
0 | 0 | 0 | 0 | 0
0 | 0 | 0 | 0 | 0
0 | 0 | 0 | 0 | 0
0 | 0 | 0 | 0 | 0
0 | 0 | 0 | 0 | 0
0 | 0 | 0 | 0 | 0
0 | 0 | 0 | 0 | 0
0 | 0 | 0 | 0 | 0
0 | 0 | 0 | 0 | 0
0 | 0 | 0 | 0 | 0
0 | 0 | 0 | 0 | 0
0 | 0 | 0 | 0 | 0
0 | 0 | 0 | 0 | 0
0 | 0 | 0 | 0 | 0
0 | 0 | 0 | 0 | 0
0 | 0 | 0 | 0 | 0
0 | 0 | 0 | 0 | 0
0 | 0 | 0 | 0 | 0
0 | 0 | 0 | 0 | 0
0 | 0 | 0 | 0 | 0
0 | 0 | 0 | 0 | 0
0 | 0 | 0 | 0 | 0
0 | 0 | 0 | 0 | 0
0 | 0 | 0 | 0 | 0
0 | 0 | 0 | 0 | 0
0 | 0 | 0 | 0 | 0
0 | 0 | 0 | 0 | 0
0 | 0 | 0 | 0 | 0
0 | 0 | 0 | 0 | 0
0 | 0 | 0 | 0 | 0
0 | 0 | 0 | 0 | 0
0 | 0 | 0 | 0 | 0
0 | 0 | 0 | 0 | 0
0 | 0 | 0 | 0 | 0
0 | 0 | 0 | 0 | 0
0 | 0 | 0 | 0 | 0
0 | 0 | 0 | 0 | 0
0 | 0 | 0 | 0 | 0
0 | 0 | 0 | 0 | 0
0 | 0 | 0 | 0 | 0
0 | 0 | 0 | 0 | 0
0 | 0 | 0 | 0 | 0
0 | 0 | 0 | 0 | 0
0 | 0 | 0 | 0 | 0
0 | 0 | 0 | 0 | 0
0 | 0 | 0 | 0 | 0
0 | 0 | 0 | 0 | 0
0 | 0 | 0 | 0 | 0
0 | 0 | 0 | 0 | 0
0 | 0 | 0 | 0 | 0
0 | 0 | 0 | 0 | 0
0 | 0 | 0 | 0 | 0
0 | 0 | 0 | 0 | 0
0 | 0 | 0 | 0 | 0
0 | 0 | 0 | 0 | 0
0 | 0 | 0 | 0 | 0
0 | 0 | 0 | 0 | 0
0 | 0 | 0 | 0 | 0
0 | 0 | 0 | 0 | 0
0 | 0 | 0 | 0 | 0
0 | 0 | 0 | 0 | 0
0 | 0 | 0 | 0 | 0
0 | 0 | 0 | 0 | 0
0 | 0 | 0 | 0 | 0
0 | 0 | 0 | 0 | 0
0 | 0 | 0 | 0 | 0
0 | 0 | 0 | 0 | 0
0 | 0 | 0 | 0 | 0
0 | 0 | 0 | 0 | 0
0 | 0 | 0 | 0 | 0
0 | 0 | 0 | 0 | 0
0 | 0 | 0 | 0 | 0
0 | 0 | 0 | 0 | 0
0 | 0 | 0 | 0 | 0
0 | 0 | 0 | 0 | 0
0 | 0 | 0 | 0 | 0
0 | 0 | 0 | 0 | 0
0 | 0 | 0 | 0 | 0
0 | 0 | 0 | 0 | 0
0 | 0 | 0 | 0 | 0
0 | 0 | 0 | 0 | 0
0 | 0 | 0 | 0 | 0
0 | 0 | 0 | 0 | 0
0 | 0 | 0 | 0 | 0
0 | 0 | 0 | 0 | 0
0 | 0 | 0 | 0 | 0
0 | 0 | 0 | 0 | 0
0 | 0 | 0 | 0 | 0
0 | 0 | 0 | 0 | 0
0 | 0 | 0 | 0 | 0
0 | 0 | 0 | 0 | 0
0 | 0 | 0 | 0 | 0
0 | 0 | 0 | 0 | 0
0 | 0 | 0 | 0 | 0
0 | 0 | 0 | 0 | 0
0 | 0 | 0 | 0 | 0
0 | 0 | 0 | 0 | 0
0 | 0 | 0 | 0 | 0
0 | 0 | 0 | 0 | 0
0 | 0 | 0 | 0 | 0
0 | 0 | 0 | 0 | 0
0 | 0 | 0 | 0 | 0
0 | 0 | 0 | 0 | 0
0 | 0 | 0 | 0 | 0
0 | 0 | 0 | 0 | 0
0 | 0 | 0 | 0 | 0
0 | 0 | 0 | 0 | 0
0 | 0 | 0 | 0 | 0
0 | 0 | 0 | 0 | 0
0 | 0 | 0 | 0 | 0
0 | 0 | 0 | 0 | 0
0 | 0 | 0 | 0 | 0
0 | 0 | 0 | 0 | 0
0 | 0 | 0 | 0 | 0
0 | 0 | 0 | 0 | 0
0 | 0 | 0 | 0 | 0
0 | 0 | 0 | 0 | 0
0 | 0 | 0 | 0 | 0
0 | 0 | 0 | 0 | 0
0 | 0 | 0 | 0 | 0
0 | 0 | 0 | 0 | 0
0 | 0 | 0 | 0 | 0
0 | 0 | 0 | 0 | 0
0 | 0 | 0 | 0 | 0
0 | 0 | 0 | 0 | 0
0 | 0 | 0 | 0 | 0
0 | 0 | 0 | 0 | 0
0 | 0 | 0 | 0 | 0
0 | 0 | 0 | 0 | 0
0 | 0 | 0 | 0 | 0
0 | 0 | 0 | 0 | 0
0 | 0 | 0 | 0 | 0
0 | 0 | 0 | 0 | 0
0 | 0 | 0 | 0 | 0
0 | 0 | 0 | 0 | 0
0 | 0 | 0 | 0 | 0
0 | 0 | 0 | 0 | 0
0 | 0 | 0 | 0 | 0
0 | 0 | 0 | 0 | 0
0 | 0 | 0 | 0 | 0
0 | 0 | 0 | 0 | 0
0 | 0 | 0 | 0 | 0
0 | 0 | 0 | 0 | 0
0 | 0 | 0 | 0 | 0
0 | 0 | 0 | 0 | 0
0 | 0 | 0 | 0 | 0
0 | 0 | 0 | 0 | 0
0 | 0 | 0 | 0 | 0
0 | 0 | 0 | 0 | 0
0 | 0 | 0 | 0 | 0
0 | 0 | 0 | 0 | 0
0 | 0 | 0 | 0 | 0
0 | 0 | 0 | 0 | 0
0 | 0 | 0 | 0 | 0
0 | 0 | 0 | 0 | 0
0 | 0 | 0 | 0 | 0
0 | 0 | 0 | 0 | 0
0 | 0 | 0 | 0 | 0
0 | 0 | 0 | 0 | 0
0 | 0 | 0 | 0 | 0
0 | 0 | 0 | 0 | 0
0 | 0 | 0 | 0 | 0
0 | 0 | 0 | 0 | 0
0 | 0 | 0 | 0 | 0
0 | 0 | 0 | 0 | 0
0 | 0 | 0 | 0 | 0
0 | 0 | 0 | 0 | 0
0 | 0 | 0 | 0 | 0
0 | 0 | 0 | 0 | 0
0 | 0 | 0 | 0 | 0
0 | 0 | 0 | 0 | 0
0 | 0 | 0 | 0 | 0
0 | 0 | 0 | 0 | 0
0 | 0 | 0 | 0 | 0
0 | 0 | 0 | 0 | 0
0 | 0 | 0 | 0 | 0
0 | 0 | 0 | 0 | 0
0 | 0 | 0 | 0 | 0
0 | 0 | 0 | 0 | 0
0 | 0 | 0 | 0 | 0
0 | 0 | 0 | 0 | 0
0 | 0 | 0 | 0 | 0
0 | 0 | 0 | 0 | 0
0 | 0 | 0 | 0 | 0
0 | 0 | 0 | 0 | 0
0 | 0 | 0 | 0 | 0
0 | 0 | 0 | 0 | 0
0 | 0 | 0 | 0 | 0
0 | 0 | 0 | 0 | 0
0 | 0 | 0 | 0 | 0
0 | 0 | 0 | 0 | 0
0 | 0 | 0 | 0 | 0
0 | 0 | 0 | 0 | 0
0 | 0 | 0 | 0 | 0
0 | 0 | 0 | 0 | 0
0 | 0 | 0 | 0 | 0
0 | 0 | 0 | 0 | 0
0 | 0 | 0 | 0 | 0
0 | 0 | 0 | 0 | 0
0 | 0 | 0 | 0 | 0
0 | 0 | 0 | 0 | 0
0 | 0 | 0 | 0 | 0
0 | 0 | 0 | 0 | 0
0 | 0 | 0 | 0 | 0
0 | 0 | 0 | 0 | 0
0 | 0 | 0 | 0 | 0
0 | 0 | 0 | 0 | 0
0 | 0 | 0 | 0 | 0
0 | 0 | 0 | 0 | 0
0 | 0 | 0 | 0 | 0
0 | 0 | 0 | 0 | 0
0 | 0 | 0 | 0 | 0
0 | 0 | 0 | 0 | 0
0 | 0 | 0 | 0 | 0
0 | 0 | 0 | 0 | 0
0 | 0 | 0 | 0 | 0
0 | 0 | 0 | 0 | 0
0 | 0 | 0 | 0 | 0
0 | 0 | 0 | 0 | 0
0 | 0 | 0 | 0 | 0
0 | 0 | 0 | 0 | 0
0 | 0 | 0 | 0 | 0
0 | 0 | 0 | 0 | 0
0 | 0 | 0 | 0 | 0
0 | 0 | 0 | 0 | 0
0 | 0 | 0 | 0 | 0
0 | 0 | 0 | 0 | 0
0 | 0 | 0 | 0 | 0
0 | 0 | 0 | 0 | 0
0 | 0 | 0 | 0 | 0
0 | 0 | 0 | 0 | 0
0 | 0 | 0 | 0 | 0
0 | 0 | 0 | 0 | 0
0 | 0 | 0 | 0 | 0
0 | 0 | 0 | 0 | 0
0 | 0 | 0 | 0 | 0
0 | 0 | 0 | 0 | 0
0 | 0 | 0 | 0 | 0
0 | 0 | 0 | 0 | 0
0 | 0 | 0 | 0 | 0
0 | 0 | 0 | 0 | 0
0 | 0 | 0 | 0 | 0
0 | 0 | 0 | 0 | 0
0 | 0 | 0 | 0 | 0
0 | 0 | 0 | 0 | 0
0 | 0 | 0 | 0 | 0
0 | 0 | 0 | 0 | 0
0 | 0 | 0 | 0 | 0
0 | 0 | 0 | 0 | 0
0 | 0 | 0 | 0 | 0
0 | 0 | 0 | 0 | 0
0 | 0 | 0 | 0 | 0
0 | 0 | 0 | 0 | 0
0 | 0 | 0 | 0 | 0
0 | 0 | 0 | 0 | 0
0 | 0 | 0 | 0 | 0
0 | 0 | 0 | 0 | 0
0 | 0 | 0 | 0 | 0
0 | 0 | 0 | 0 | 0
0 | 0 | 0 | 0 | 0
0 | 0 | 0 | 0 | 0
0 | 0 | 0 | 0 | 0
0 | 0 | 0 | 0 | 0
0 | 0 | 0 | 0 | 0
0 | 0 | 0 | 0 | 0
0 | 0 | 0 | 0 | 0
0 | 0 | 0 | 0 | 0
0 | 0 | 0 | 0 | 0
0 | 0 | 0 | 0 | 0
0 | 0 | 0 | 0 | 0
0 | 0 | 0 | 0 | 0
0 | 0 | 0 | 0 | 0
0 | 0 | 0 | 0 | 0
0 | 0 | 0 | 0 | 0
0 | 0 | 0 | 0 | 0
0 | 0 | 0 | 0 | 0
0 | 0 | 0 | 0 | 0
0 | 0 | 0 | 0 | 0
0 | 0 | 0 | 0 | 0
0 | 0 | 0 | 0 | 0
0 | 0 | 0 | 0 | 0
0 | 0 | 0 | 0 | 0
0 | 0 | 0 | 0 | 0
0 | 0 | 0 | 0 | 0
0 | 0 | 0 | 0 | 0
0 | 0 | 0 | 0 | 0
0 | 0 | 0 | 0 | 0
0 | 0 | 0 | 0 | 0
0 | 0 | 0 | 0 | 0
0 | 0 | 0 | 0 | 0
0 | 0 | 0 | 0 | 0
0 | 0 | 0 | 0 | 0
0 | 0 | 0 | 0 | 0
0 | 0 | 0 | 0 | 0
0 | 0 | 0 | 0 | 0
0 | 0 | 0 | 0 | 0
0 | 0 | 0 | 0 | 0
0 | 0 | 0 | 0 | 0
0 | 0 | 0 | 0 | 0
0 | 0 | 0 | 0 | 0
0 | 0 | 0 | 0 | 0
0 | 0 | 0 | 0 | 0
0 | 0 | 0 | 0 | 0
0 | 0 | 0 | 0 | 0
0 | 0 | 0 | 0 | 0
0 | 0 | 0 | 0 | 0
0 | 0 | 0 | 0 | 0
0 | 0 | 0 | 0 | 0
0 | 0 | 0 | 0 | 0
0 | 0 | 0 | 0 | 0
0 | 0 | 0 | 0 | 0
0 | 0 | 0 | 0 | 0
0 | 0 | 0 | 0 | 0
0 | 0 | 0 | 0 | 0
0 | 0 | 0 | 0 | 0
0 | 0 | 0 | 0 | 0
0 | 0 | 0 | 0 | 0
0 | 0 | 0 | 0 | 0
0 | 0 | 0 | 0 | 0
0 | 0 | 0 | 0 | 0
0 | 0 | 0 | 0 | 0
0 | 0 | 0 | 0 | 0
0 | 0 | 0 | 0 | 0
0 | 0 | 0 | 0 | 0
0 | 0 | 0 | 0 | 0
0 | 0 | 0 | 0 | 0
0 | 0 | 0 | 0 | 0
0 | 0 | 0 | 0 | 0
0 | 0 | 0 | 0 | 0
0 | 0 | 0 | 0 | 0
0 | 0 | 0 | 0 | 0
0 | 0 | 0 | 0 | 0
0 | 0 | 0 | 0 | 0
0 | 0 | 0 | 0 | 0
0 | 0 | 0 | 0 | 0
0 | 0 | 0 | 0 | 0
0 | 0 | 0 | 0 | 0
0 | 0 | 0 | 0 | 0
0 | 0 | 0 | 0 | 0
0 | 0 | 0 | 0 | 0
0 | 0 | 0 | 0 | 0
0 | 0 | 0 | 0 | 0
0 | 0 | 0 | 0 | 0
0 | 0 | 0 | 0 | 0
0 | 0 | 0 | 0 | 0
0 | 0 | 0 | 0 | 0
0 | 0 | 0 | 0 | 0
0 | 0 | 0 | 0 | 0
0 | 0 | 0 | 0 | 0
0 | 0 | 0 | 0 | 0
0 | 0 | 0 | 0 | 0
0 | 0 | 0 | 0 | 0
0 | 0 | 0 | 0 | 0
0 | 0 | 0 | 0 | 0
0 | 0 | 0 | 0 | 0
0 | 0 | 0 | 0 | 0
0 | 0 | 0 | 0 | 0
0 | 0 | 0 | 0 | 0
0 | 0 | 0 | 0 | 0
0 | 0 | 0 | 0 | 0
0 | 0 | 0 | 0 | 0
0 | 0 | 0 | 0 | 0
0 | 0 | 0 | 0 | 0
0 | 0 | 0 | 0 | 0
0 | 0 | 0 | 0 | 0
0 | 0 | 0 | 0 | 0
0 | 0 | 0 | 0 | 0
0 | 0 | 0 | 0 | 0
0 | 0 | 0 | 0 | 0
0 | 0 | 0 | 0 | 0
0 | 0 | 0 | 0 | 0
0 | 0 | 0 | 0 | 0
0 | 0 | 0 | 0 | 0
0 | 0 | 0 | 0 | 0
0 | 0 | 0 | 0 | 0
0 | 0 | 0 | 0 | 0
0 | 0 | 0 | 0 | 0
0 | 0 | 0 | 0 | 0
0 | 0 | 0 | 0 | 0
0 | 0 | 0 | 0 | 0
0 | 0 | 0 | 0 | 0
0 | 0 | 0 | 0 | 0
0 | 0 | 0 | 0 | 0
0 | 0 | 0 | 0 | 0
0 | 0 | 0 | 0 | 0
0 | 0 | 0 | 0 | 0
0 | 0 | 0 | 0 | 0
0 | 0 | 0 | 0 | 0
0 | 0 | 0 | 0 | 0
0 | 0 | 0 | 0 | 0
0 | 0 | 0 | 0 | 0
0 | 0 | 0 | 0 | 0
0 | 0 | 0 | 0 | 0
0 | 0 | 0 | 0 | 0
0 | 0 | 0 | 0 | 0
0 | 0 | 0 | 0 | 0
0 | 0 | 0 | 0 | 0
0 | 0 | 0 | 0 | 0
0 | 0 | 0 | 0 | 0
0 | 0 | 0 | 0 | 0
0 | 0 | 0 | 0 | 0
0 | 0 | 0 | 0 | 0
0 | 0 | 0 | 0 | 0
0 | 0 | 0 | 0 | 0
0 | 0 | 0 | 0 | 0
0 | 0 | 0 | 0 | 0
0 | 0 | 0 | 0 | 0
0 | 0 | 0 | 0 | 0
0 | 0 | 0 | 0 | 0
0 | 0 | 0 | 0 | 0
0 | 0 | 0 | 0 | 0
0 | 0 | 0 | 0 | 0
0 | 0 | 0 | 0 | 0
0 | 0 | 0 | 0 | 0
0 | 0 | 0 | 0 | 0
0 | 0 | 0 | 0 | 0
0 | 0 | 0 | 0 | 0
0 | 0 | 0 | 0 | 0
0 | 0 | 0 | 0 | 0
0 | 0 | 0 | 0 | 0
0 | 0 | 0 | 0 | 0
0 | 0 | 0 | 0 | 0
0 | 0 | 0 | 0 | 0
0 | 0 | 0 | 0 | 0
0 | 0 | 0 | 0 | 0
0 | 0 | 0 | 0 | 0
0 | 0 | 0 | 0 | 0
0 | 0 | 0 | 0 | 0
0 | 0 | 0 | 0 | 0
0 | 0 | 0 | 0 | 0
0 | 0 | 0 | 0 | 0
0 | 0 | 0 | 0 | 0
0 | 0 | 0 | 0 | 0
0 | 0 | 0 | 0 | 0
0 | 0 | 0 | 0 | 0
0 | 0 | 0 | 0 | 0
0 | 0 | 0 | 0 | 0
0 | 0 | 0 | 0 | 0
0 | 0 | 0 | 0 | 0
0 | 0 | 0 | 0 | 0
0 | 0 | 0 | 0 | 0
0 | 0 | 0 | 0 | 0
0 | 0 | 0 | 0 | 0
0 | 0 | 0 | 0 | 0
0 | 0 | 0 | 0 | 0
0 | 0 | 0 | 0 | 0
0 | 0 | 0 | 0 | 0
0 | 0 | 0 | 0 | 0
0 | 0 | 0 | 0 | 0
0 | 0 | 0 | 0 | 0
0 | 0 | 0 | 0 | 0
0 | 0 | 0 | 0 | 0
0 | 0 | 0 | 0 | 0
0 | 0 | 0 | 0 | 0
0 | 0 | 0 | 0 | 0
0 | 0 | 0 | 0 | 0
0 | 0 | 0 | 0 | 0
0 | 0 | 0 | 0 | 0
0 | 0 | 0 | 0 | 0
0 | 0 | 0 | 0 | 0
0 | 0 | 0 | 0 | 0
0 | 0 | 0 | 0 | 0
0 | 0 | 0 | 0 | 0
0 | 0 | 0 | 0 | 0
0 | 0 | 0 | 0 | 0
0 | 0 | 0 | 0 | 0
0 | 0 | 0 | 0 | 0
0 | 0 | 0 | 0 | 0
0 | 0 | 0 | 0 | 0
0 | 0 | 0 | 0 | 0
0 | 0 | 0 | 0 | 0
0 | 0 | 0 | 0 | 0
0 | 0 | 0 | 0 | 0
0 | 0 | 0 | 0 | 0
0 | 0 | 0 | 0 | 0
0 | 0 | 0 | 0 | 0
0 | 0 | 0 | 0 | 0
0 | 0 | 0 | 0 | 0
0 | 0 | 0 | 0 | 0
0 | 0 | 0 | 0 | 0
0 | 0 | 0 | 0 | 0
0 | 0 | 0 | 0 | 0
0 | 0 | 0 | 0 | 0
0 | 0 | 0 | 0 | 0
0 | 0 | 0 | 0 | 0
0 | 0 | 0 | 0 | 0
0 | 0 | 0 | 0 | 0
0 | 0 | 0 | 0 | 0
0 | 0 | 0 | 0 | 0
0 | 0 | 0 | 0 | 0
0 | 0 | 0 | 0 | 0
0 | 0 | 0 | 0 | 0
0 | 0 | 0 | 0 | 0
0 | 0 | 0 | 0 | 0
0 | 0 | 0 | 0 | 0
0 | 0 | 0 | 0 | 0
0 | 0 | 0 | 0 | 0
0 | 0 | 0 | 0 | 0
0 | 0 | 0 | 0 | 0
0 | 0 | 0 | 0 | 0
0 | 0 | 0 | 0 | 0
0 | 0 | 0 | 0 | 0
0 | 0 | 0 | 0 | 0
0 | 0 | 0 | 0 | 0
0 | 0 | 0 | 0 | 0
0 | 0 | 0 | 0 | 0
0 | 0 | 0 | 0 | 0
0 | 0 | 0 | 0 | 0
0 | 0 | 0 | 0 | 0
0 | 0 | 0 | 0 | 0
0 | 0 | 0 | 0 | 0
0 | 0 | 0 | 0 | 0
0 | 0 | 0 | 0 | 0
0 | 0 | 0 | 0 | 0
0 | 0 | 0 | 0 | 0
0 | 0 | 0 | 0 | 0
0 | 0 | 0 | 0 | 0
0 | 0 | 0 | 0 | 0
0 | 0 | 0 | 0 | 0
0 | 0 | 0 | 0 | 0
0 | 0 | 0 | 0 | 0
0 | 0 | 0 | 0 | 0
0 | 0 | 0 | 0 | 0
0 | 0 | 0 | 0 | 0
0 | 0 | 0 | 0 | 0
0 | 0 | 0 | 0 | 0
0 | 0 | 0 | 0 | 0
0 | 0 | 0 | 0 | 0
0 | 0 | 0 | 0 | 0
0 | 0 | 0 | 0 | 0
0 | 0 | 0 | 0 | 0
0 | 0 | 0 | 0 | 0
0 | 0 | 0 | 0 | 0
0 | 0 | 0 | 0 | 0
0 | 0 | 0 | 0 | 0
0 | 0 | 0 | 0 | 0
0 | 0 | 0 | 0 | 0

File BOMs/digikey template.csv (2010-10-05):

Digi-Key Part No. | Manufacturer Name | Mfr Part No. | Customer Reference | Qty1 | Qty2 | Qty3
MC9S12XDP512MAL-ND |  |  | REF1 | 2
-- |  |  |  | 2
LM1949N-ND |  |  | REF3 | 8
-- |  |  |  | 8
490-1666-2-ND |  |  |  | 3,000
311-1099-1-ND |  |  |  | 100
WHCR10FECT-ND |  |  |  | 8
RMCF0603JT270RCT-ND |  |  |  | 100
RMCF0603JT1K00CT-ND |  |  |  | 100
RMCF0603JT2K20CT-ND |  |  |  | 100
RMCF0603JT3K30CT-ND |  |  |  | 100
RMCF0603JT4K70CT-ND |  |  |  | 100
RMCF0603JT5K60CT-ND |  |  |  | 100
RMCF0603JT10K0CT-ND |  |  |  | 100
--
--
RMCF0603JT22K0CT-ND |  |  |  | 100
P39KGCT-ND |  |  |  | 100
RMCF0603JT68K0CT-ND |  |  |  | 100
RMCF0603JT100KCT-ND |  |  |  | 100
P680KGCT-ND |  |  |  | 100
P1.6MGCT-ND |  |  |  | 100
RMCF0603JT10M0CT-ND |  |  |  | 100
LM1815M-ND |  |  |  | 4
MAX9924UAUB+-ND |  |  |  | 2
LM2940T-5.0-ND |  |  |  | 3
LM2936MX-5.0CT-ND |  |  |  | 2
--
768-1007-1-ND |  |  |  | 2
535-9948-1-ND |  |  |  | 2
WK6242-ND |  |  |  | 10

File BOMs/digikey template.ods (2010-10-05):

Digi-Key Part No. | Manufacturer Name | Mfr Part No. | Customer Reference | Qty1 | Qty2 | Qty3
MC9S12XDP512MAL-ND |  | MC9S12XDP512MAL-ND | REF1 | 2
-- |  | -- |  | 2
LM1949N-ND |  | LM1949N-ND | REF3 | 8
-- |  | -- |  | 8
490-1666-2-ND |  | 490-1666-2-ND |  | 3,000
311-1099-1-ND |  | 311-1099-1-ND |  | 100
WHCR10FECT-ND |  | WHCR10FECT-ND |  | 8
RMCF0603JT270RCT-ND |  | RMCF0603JT270RCT-ND |  | 100
RMCF0603JT1K00CT-ND |  | RMCF0603JT1K00CT-ND |  | 100
RMCF0603JT2K20CT-ND |  | RMCF0603JT2K20CT-ND |  | 100
RMCF0603JT3K30CT-ND |  | RMCF0603JT3K30CT-ND |  | 100
RMCF0603JT4K70CT-ND |  | RMCF0603JT4K70CT-ND |  | 100
RMCF0603JT5K60CT-ND |  | RMCF0603JT5K60CT-ND |  | 100
RMCF0603JT10K0CT-ND |  | RMCF0603JT10K0CT-ND |  | 100
-- |  | --
-- |  | --
RMCF0603JT22K0CT-ND |  | RMCF0603JT22K0CT-ND |  | 100
P39KGCT-ND |  | P39KGCT-ND |  | 100
RMCF0603JT68K0CT-ND |  | RMCF0603JT68K0CT-ND |  | 100
RMCF0603JT100KCT-ND |  | RMCF0603JT100KCT-ND |  | 100
P680KGCT-ND |  | P680KGCT-ND |  | 100
P1.6MGCT-ND |  | P1.6MGCT-ND |  | 100
RMCF0603JT10M0CT-ND |  | RMCF0603JT10M0CT-ND |  | 100
LM1815M-ND |  | LM1815M-ND |  | 4
MAX9924UAUB+-ND |  | MAX9924UAUB+-ND |  | 2
LM2940T-5.0-ND |  | LM2940T-5.0-ND |  | 3
LM2936MX-5.0CT-ND |  | LM2936MX-5.0CT-ND |  | 2
-- |  | --
768-1007-1-ND |  | 768-1007-1-ND |  | 2
535-9948-1-ND |  | 535-9948-1-ND |  | 2
WK6242-ND |  | WK6242-ND |  | 10

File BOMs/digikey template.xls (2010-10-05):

Digi-Key Part No. | Manufacturer Name | Mfr Part No. | Customer Reference | Qty1 | Qty2 | Qty3
 |  | P111 | REF1 | 10
 |  | A1000 |  | 1000
 |  | P452 | REF3 | 2000

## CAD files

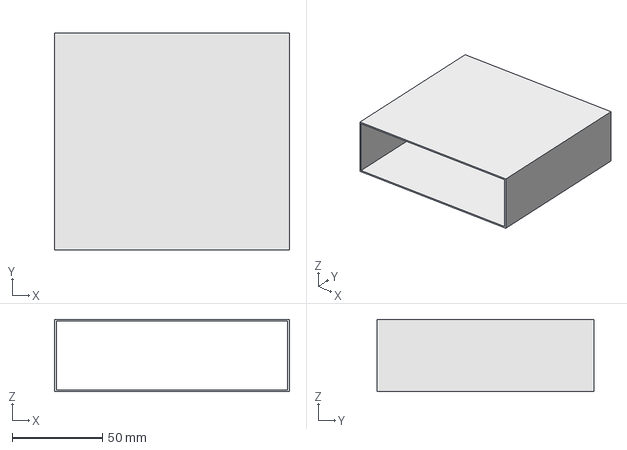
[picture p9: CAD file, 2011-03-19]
design/case/case_v0.01.fcstd
130.0 x 120.0 x 40.0 mm

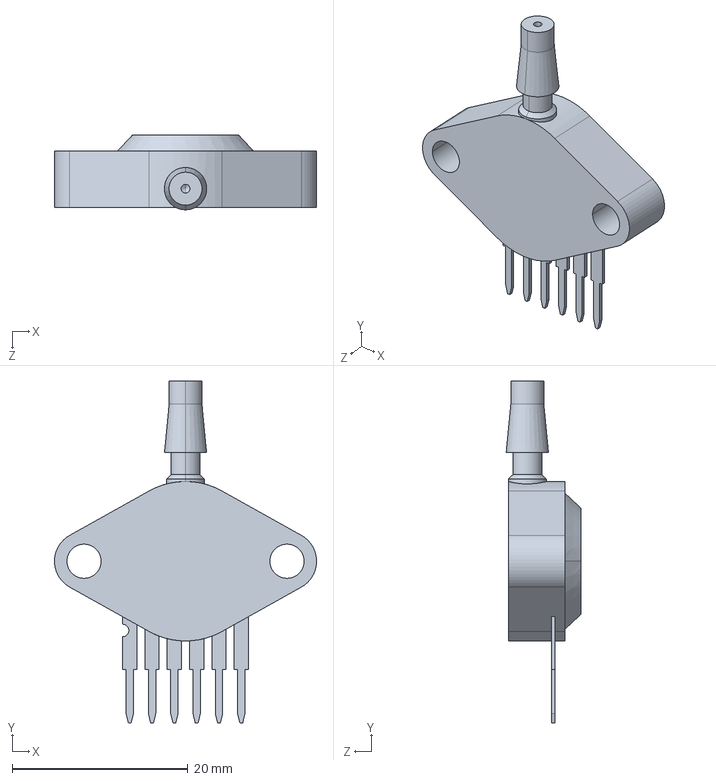
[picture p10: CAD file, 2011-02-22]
PCB-modules/MPX4100A/UNIBODY_CELL.STEP
29.8 x 38.9 x 8.51 mm

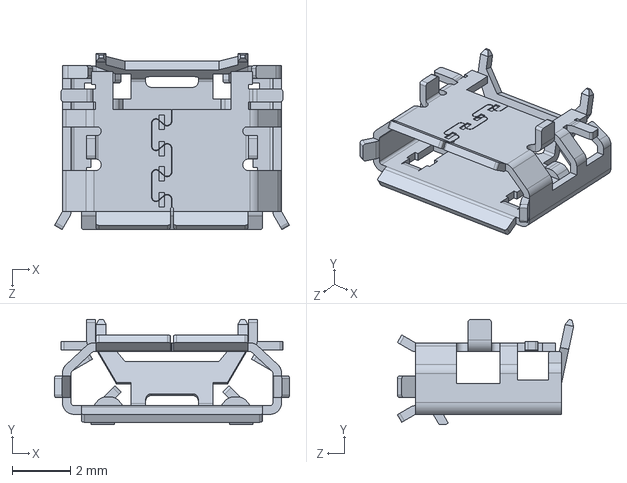
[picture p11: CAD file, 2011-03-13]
PCB-modules/usb_micro/i10103594/SHIELD1.STEP
8.04 x 3.60 x 6.03 mm

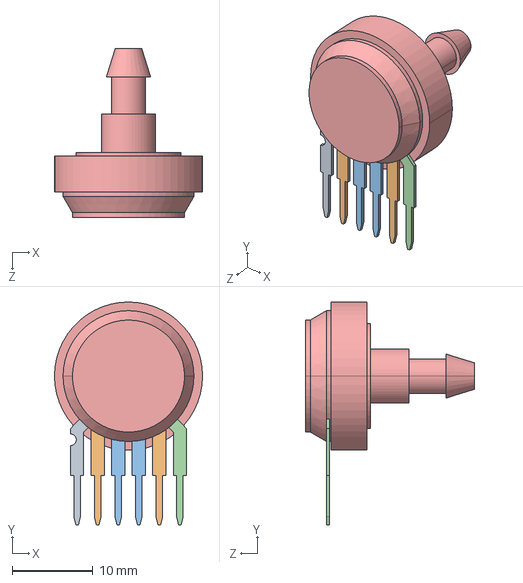
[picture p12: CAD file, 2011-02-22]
PCB-modules/MPX4100A/UNIBODY_STOVEPIPE.STEP
18.3 x 27.6 x 20.9 mm

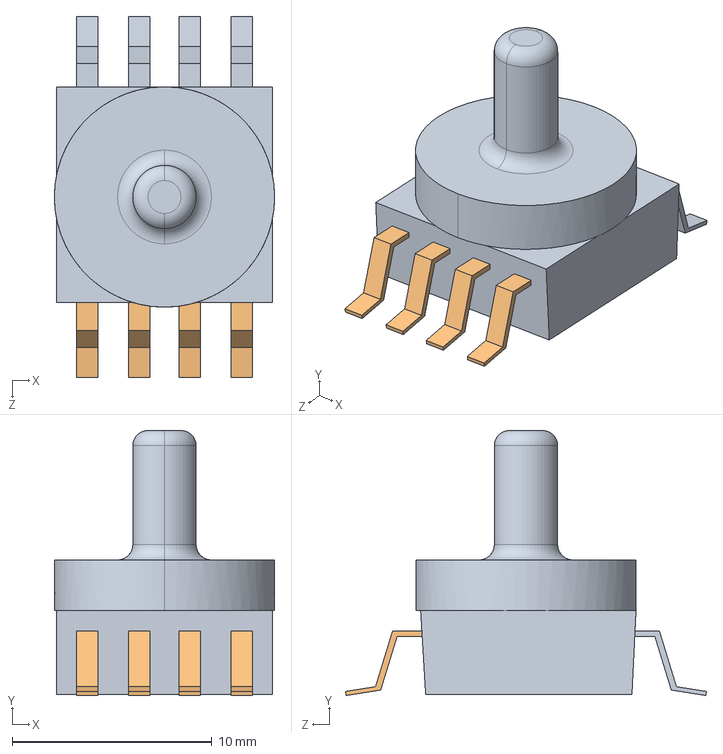
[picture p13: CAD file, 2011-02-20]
PCB-modules/MPX4100A/UNIBODY_SMALL-SMT.STEP
11.0 x 13.3 x 18.1 mm

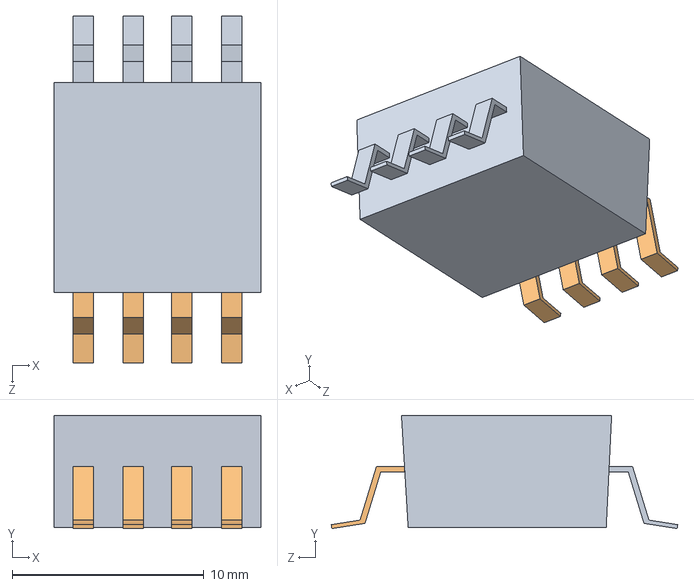
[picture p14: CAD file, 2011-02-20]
PCB-modules/MPX4100A/UNIBODY_SMT.STEP
10.8 x 5.90 x 18.1 mm

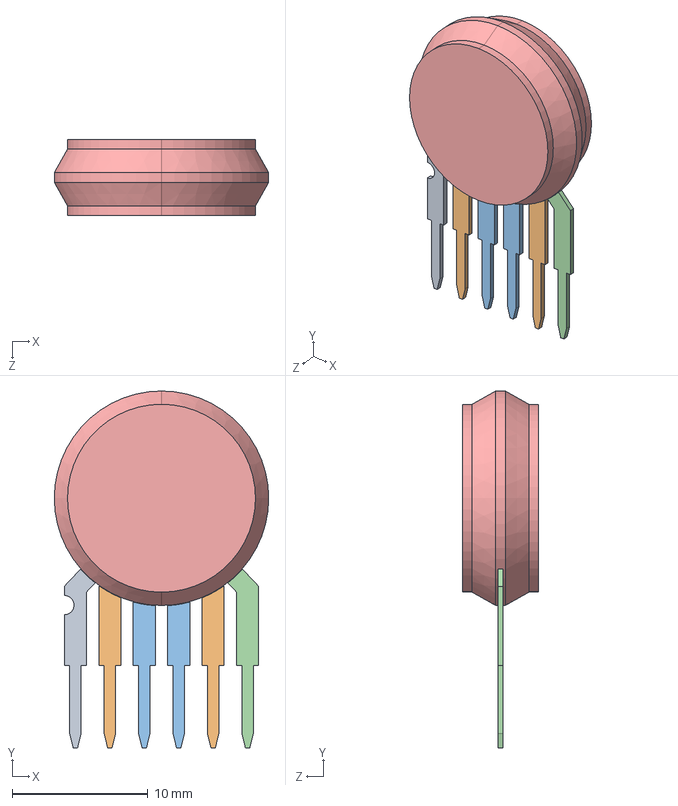
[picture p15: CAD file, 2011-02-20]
PCB-modules/MPX4100A/UNIBODY.STEP
15.8 x 26.3 x 5.59 mm

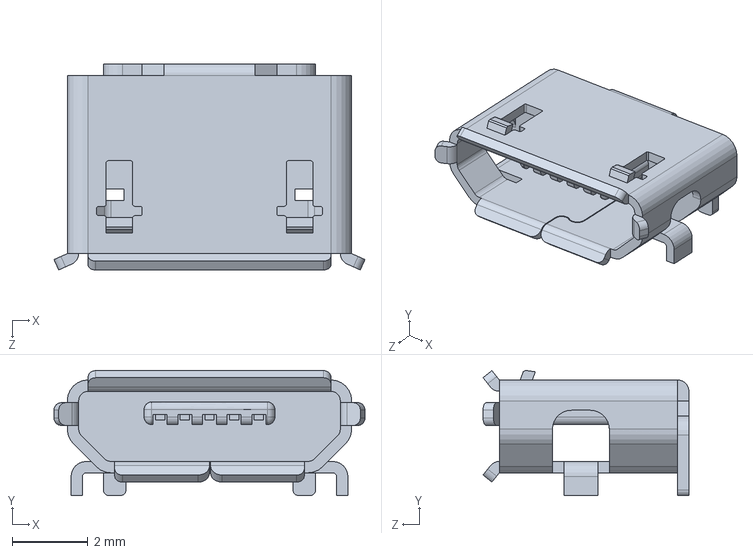
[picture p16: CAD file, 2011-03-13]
PCB-modules/USB uB/105017-0001_igs/1050170001.SLDPRT
8.20 x 3.30 x 5.43 mm

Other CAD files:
PCB-modules/usb_micro/i10103594/SUS_PLATE.sldprt
PCB-modules/usb_micro/i10103594/SUS_PLATE1.sldprt
PCB-modules/usb_micro/i10103594/MICRO-USB-SCOKET-HOUSING1.sldprt
PCB-modules/usb_micro/i10103594/SHIELD12.sldprt
PCB-modules/usb_micro/i10103594/SHIELD.sldprt
PCB-modules/usb_micro/i10103594/MICRO-USB-SCOKET-INSERT-TML1.sldprt
PCB-modules/usb_micro/i10103594/SHIELD11.SLDPRT
PCB-modules/usb_micro/i10103594/MICRO-USB-SCOKET-INSERT-TML.sldprt
PCB-modules/usb_micro/i10103594/MICRO-USB-SCOKET-HOUSING.sldprt
PCB-modules/usb_micro/i10103594/10103595.sldasm
PCB-modules/MPX4100A/UNIBODY.SLDDRW
PCB-modules/MPX4100A/UNIBODY.SLDPRT
PCB-modules/MPX4100A/UNIBODY.STL
PCB-modules/MPX4100A/UNIBODY_CELL.SLDDRW
PCB-modules/MPX4100A/UNIBODY_CELL.SLDPRT
PCB-modules/MPX4100A/UNIBODY_CELL.STL
PCB-modules/MPX4100A/UNIBODY_SMALL-SMT.SLDPRT
PCB-modules/MPX4100A/UNIBODY_SMALL-SMT.STL
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

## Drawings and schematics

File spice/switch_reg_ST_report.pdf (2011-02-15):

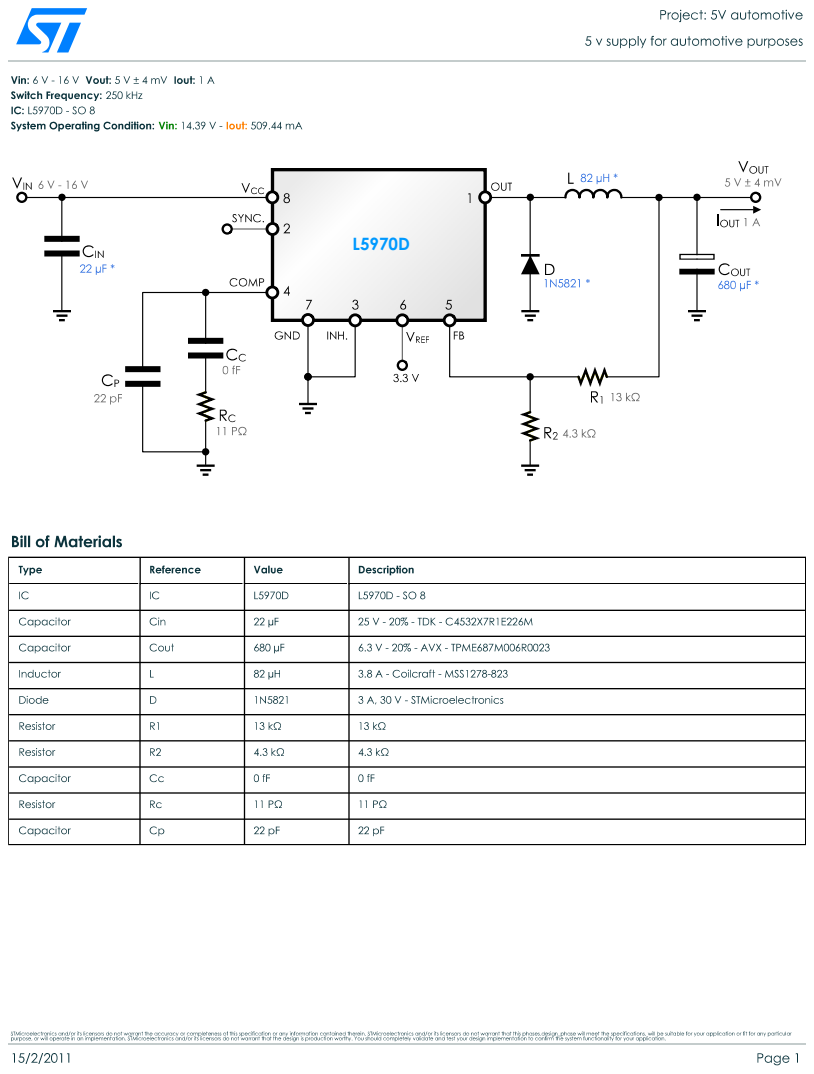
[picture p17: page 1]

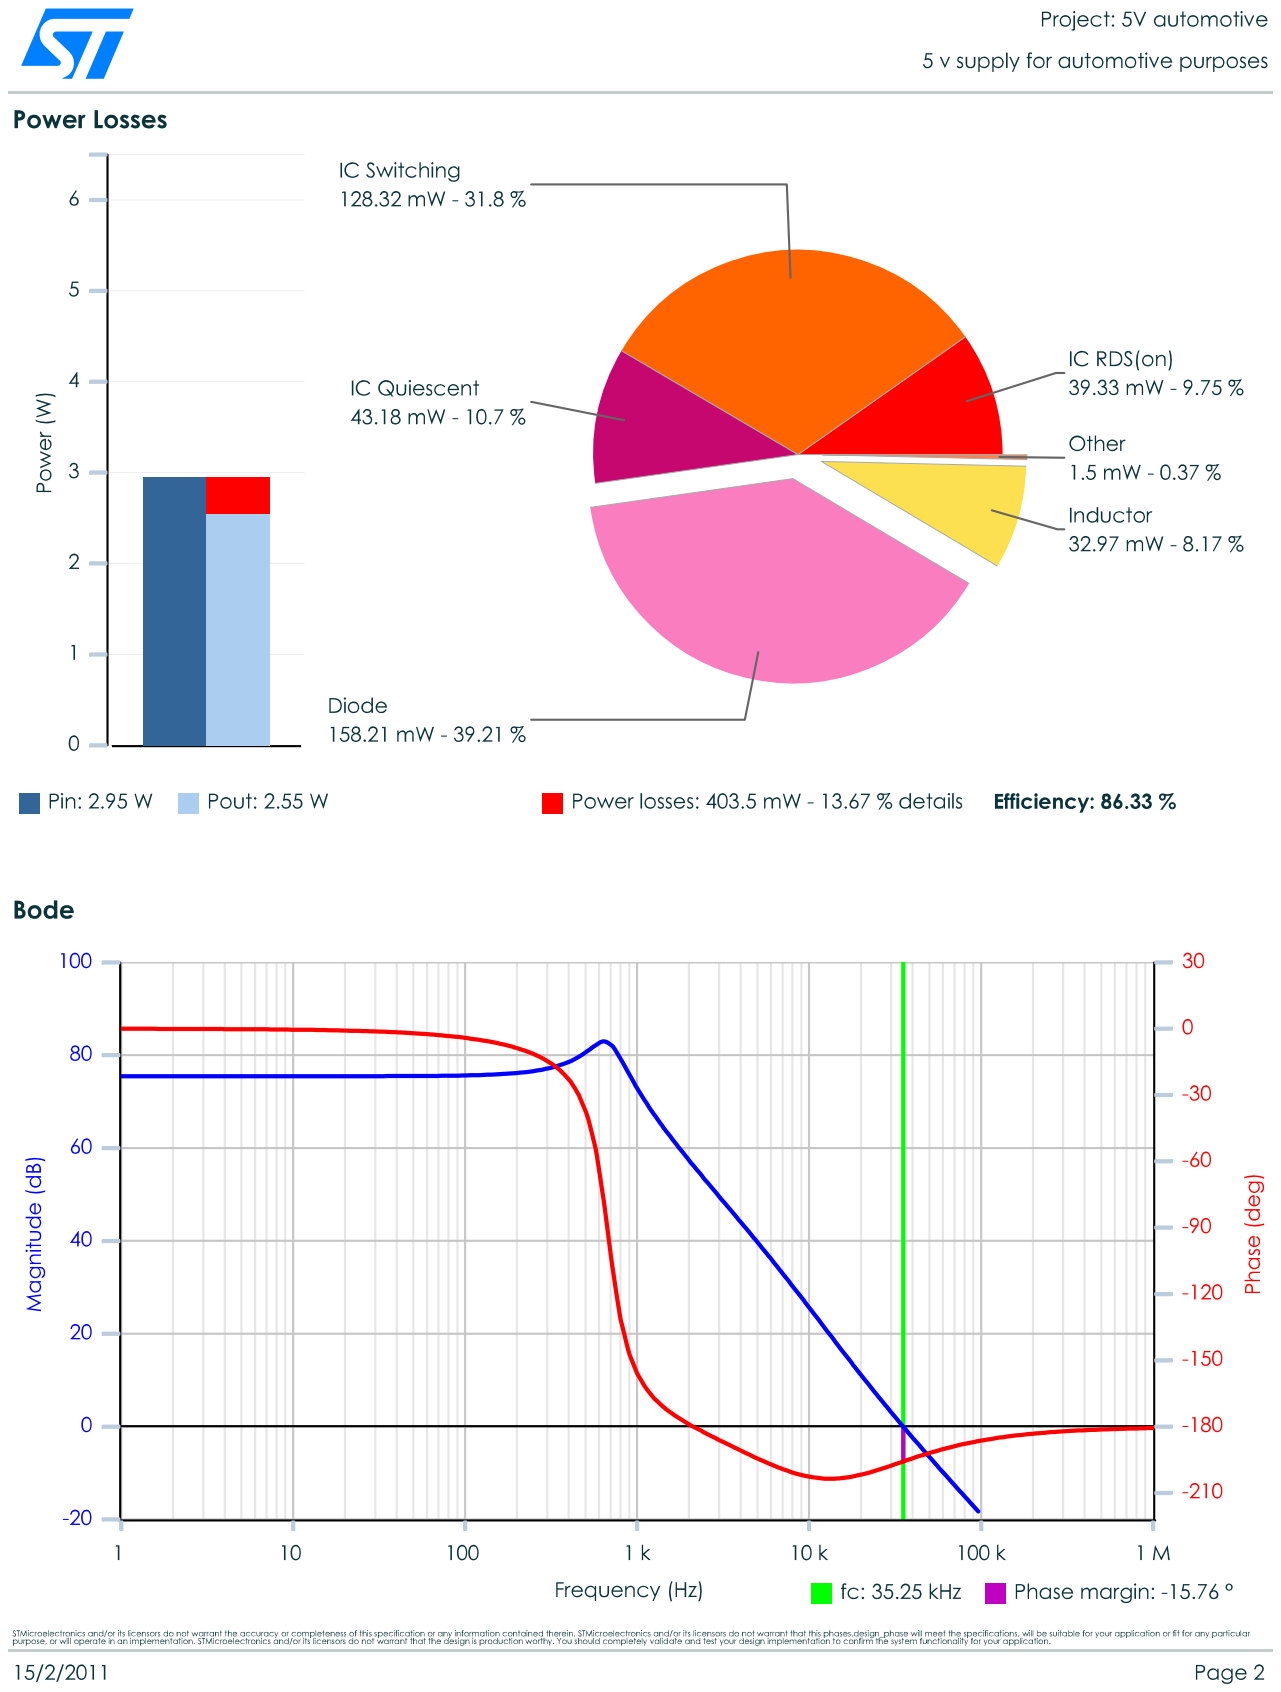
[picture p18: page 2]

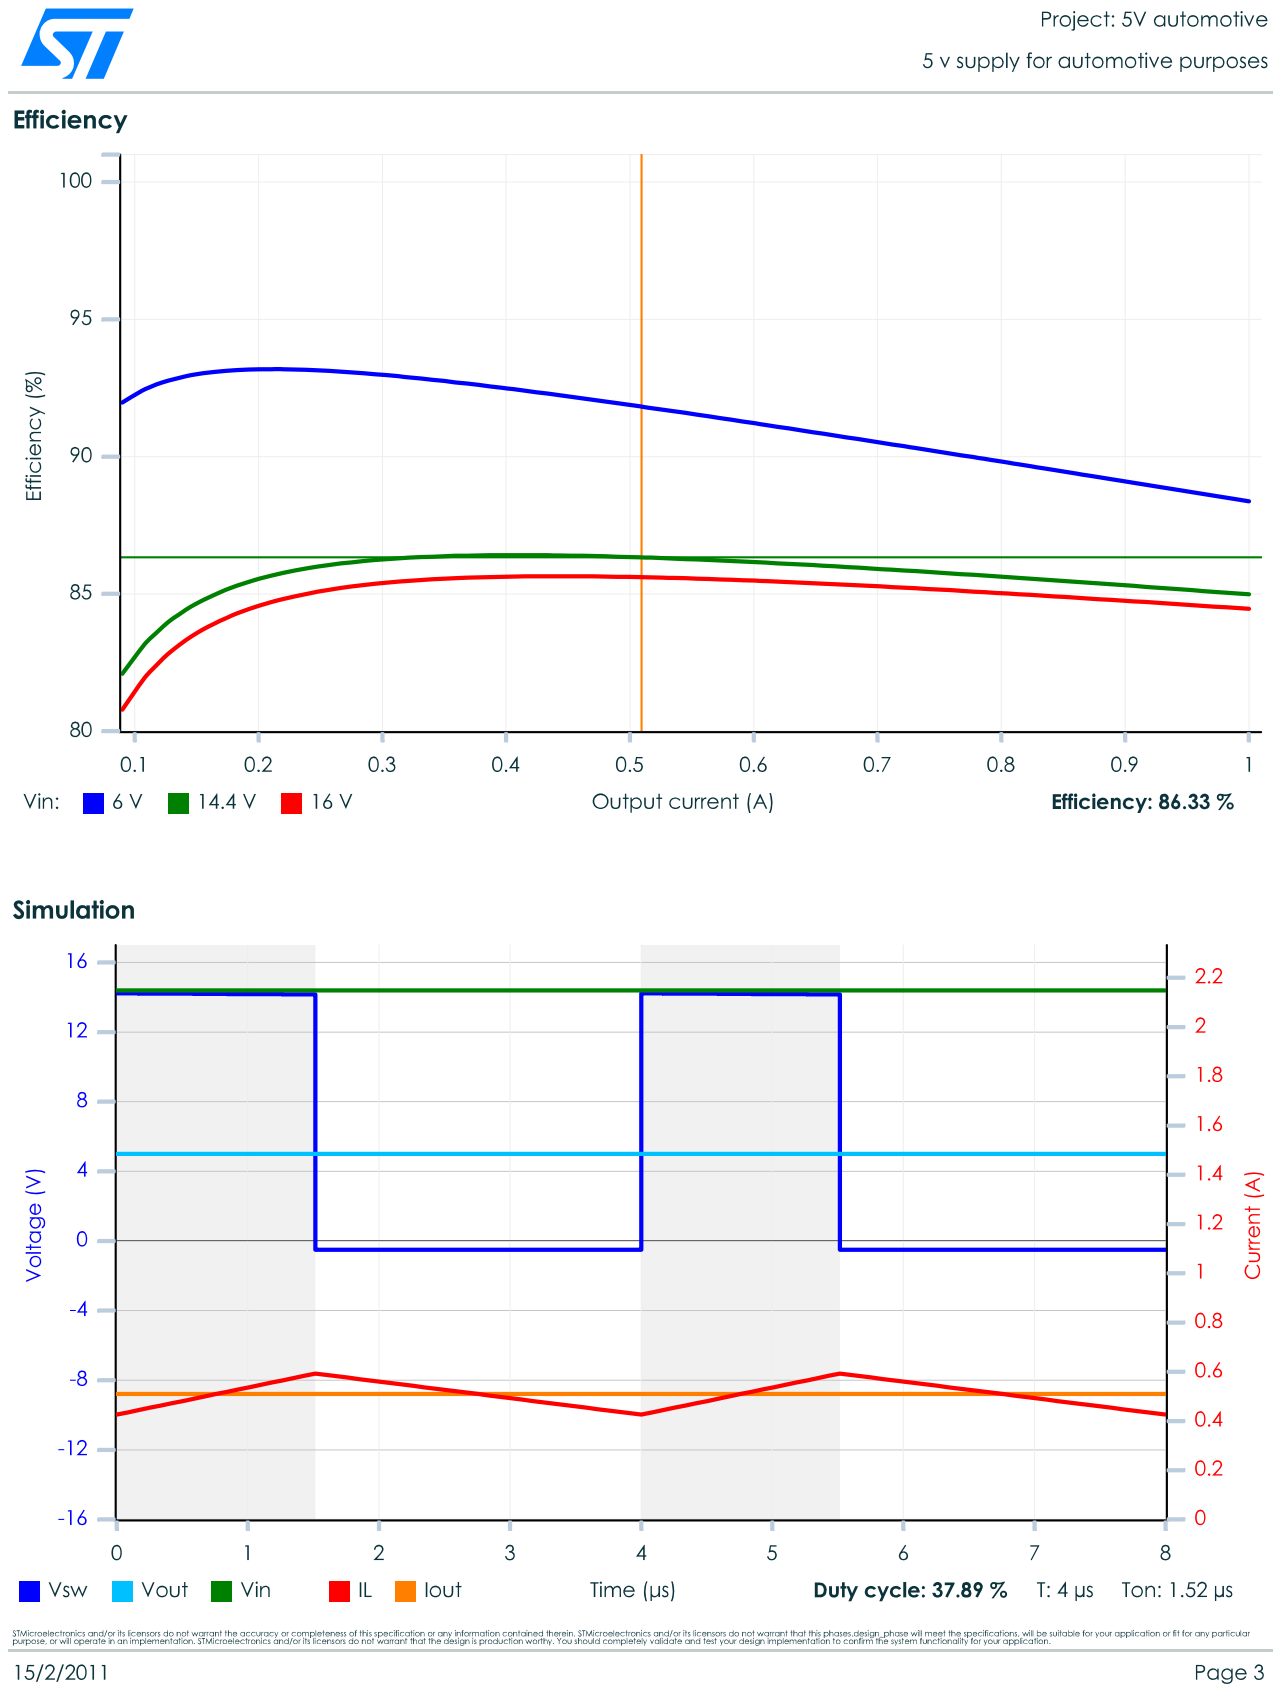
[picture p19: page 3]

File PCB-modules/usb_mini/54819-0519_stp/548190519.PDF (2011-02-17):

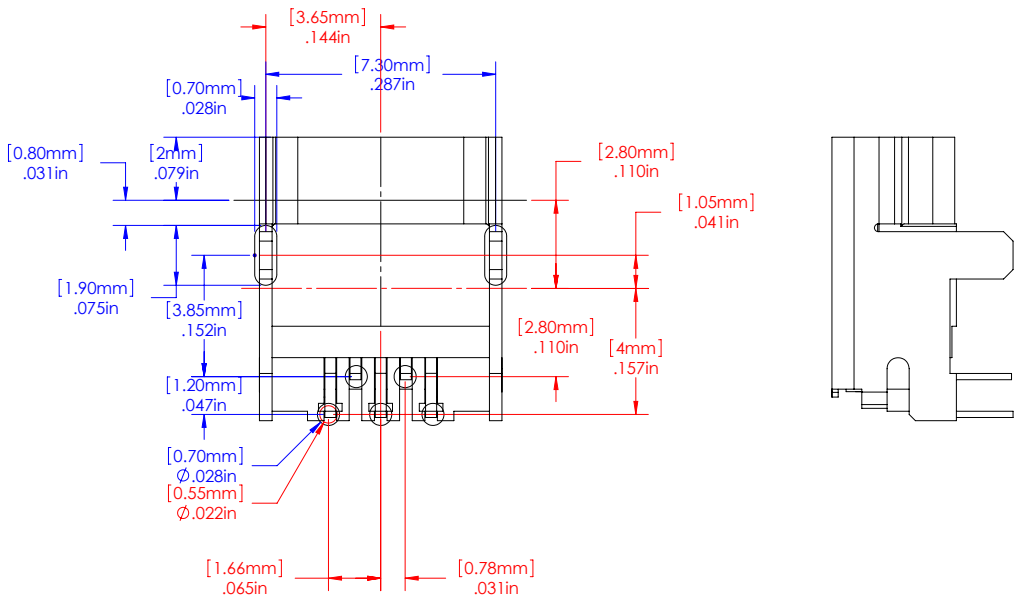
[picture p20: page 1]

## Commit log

2010-07-02 Removed LM1815 options. Now adaptive mode and square waves are the default,
    [BAT_condition.sch, CPU.sch, MAP_input1.sch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]
2010-07-03 Changed MOSFET injector driver in favor of P&H driver. Also, .gitignored .bak files. The netlist is screwed, so im going to reannotate the schematic, and associate components with SMD footprints
    [BAT_condition.sch, CPU.sch, MAP_input1.sch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]
2010-07-03 Implemented P&H, removed current sense circuitry, removed all unnecessary files from the repo
    [BAT_condition.sch, CPU.sch, MAP_input1.sch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]
2010-07-03 Corrected ERC errors by fixing the custom FreeEMS components pinouts
    [BAT_condition.sch, CPU.sch, MAP_input_1.sch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]
2010-07-03 PCB redesign. Only P&H is layeed down.
    [$savepcb.brd, BAT_condition.sch, CPU.sch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]
2010-07-22 Exchanged current sensing with peak&hold, and a closer approach to a more integrated design.
    [$savepcb.brd, BAT_condition.sch, CPU.sch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]
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2010-08-02 Created micorcontroller part, and started to design the board brain, and the serial-usb converter
    [BAT_condition.sch, CPU.sch, FreeEMS_1.0_A20.P01_1cyl_complete.csv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]
2010-08-05 Added cpu module, still many things to be connected. Changed the power supplies, now has an uototive-grade and a smaller for alaog things
    [BAT_condition.sch, CPU.sch, MAP_input_1.sch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]
2010-08-06 Everything laid down, but I still need to decide what to do with the ignition driver
    [BAT_condition.sch, CPU.sch, MAP_input_1.sch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]
2010-08-07 Routed the analog part. Added ground planes for analog and digital circutry
    [BAT_condition.sch, CPU.sch, MAP_input_1.sch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]
2010-08-15 new ignition circuit, new usb-serial IC WARNING: The FT232RL doesnt support 125deg C
    [BAT_condition.sch, CPU.sch, MAP_input_1.sch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]
2010-08-29 now with 8 low Z injector drivers, BDM connector, FT232RL. 3 grounds: digital and analog, and power (isolated). I have to remove 2 ign drivers and rearrange the connector board pins.
    [BAT_condition.sch, CPU.sch, MAP_input_1.sch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]
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2010-09-04 removed the important sch DRC errors, moved one diode in the pcb
    [BAT_condition.sch, CPU.sch, MAP_input_1.sch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]
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2010-10-05 Im decided about the components, no further changes will be made in that subject. Power regulators were moved, one supplies the cpu, the other everything else. MAX9926 is from now on the magnetic rel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
    [BAT_condition.sch, BOM.ods, CPU.sch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]
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2010-10-24 Injector drivers, ignition drivers, stepper, and most of the analog circuits routed
    [BAT_condition.sch, CPU.sch, MAP_input_1.sch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]
2010-10-29 Added signal connector in a proper way, modified analog ground plane, still not convinced about it. board almost routed
    [BAT_condition.sch, CPU.sch, MAF_input.sch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]
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2010-11-10 Project renamed; from now on this design will be known as the puma board for FreeEMS
    [BAT_condition.sch, CPU.sch, MAF_input.sch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]
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2010-12-18 6 CPU pins (PT6,PT7,PM0,PM1,PM2,PM3) routed to the 40-pin header. Improved ground planes
    [BAT_condition.sch, CPU.sch, MAF_input.sch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]
2010-12-20 Separated many resistors to have some soldermask between them. Minor doc fixes
    [puma.brd]
2010-12-24 More silkscreens done, and some connectors labeling. A script to create pads from images is also included
    [puma.brd]
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2010-12-26 Included Jarveys changes, added labels, logos, zero current ring, increased hole sizes, tested DRC, added a couple of test points for the MCU
    [BAT_condition.sch, CPU.sch, FreeEMS_1.0_A20.P01_1cyl_complete.csv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]
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2010-12-27 exchanged MAP for AAP and viceversa, added gnd,5v and out to U5 and U6
    [puma.brd]
2010-12-27 More silkscreen work, many nets named/defined, injector leds added, kicads DRC passed
    [BAT_condition.sch, CPU.sch, MAF_input.sch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]
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2010-12-30 VDDPLL is now tied to 5v, and it wasnt. It is "Spin1 known error 1". BOM is more complete now
    [BAT_condition.sch, CPU.sch, MAF_input.sch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]
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2010-12-31 Added capacitors and diodes to the BOM. All LEDs are red for now.
    [BAT_condition.sch, CPU.sch, MAF_input.sch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]
2011-01-01 BOM completed! Now it can be generated automatically, although some format tweaks have to be done for a clean Digikey upload
    [BAT_condition.sch, CPU.sch, MAF_input.sch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]
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2011-01-06 VDD1, VDD2, and VDDPLL are correct now.
    [BAT_condition.sch, CPU.sch, MAF_input.sch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]
2011-01-12 This is a just-in-case commit, so jharvey can make his own modifications with freedom.
    [puma.brd]
2011-01-22 Includes a script to update all components information, and a more verbose BOM
    [BAT_condition.sch, CPU.sch, FreeEMS_1.0_A20.P01_1cyl_complete.csv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]
2011-01-22 Fixed MAP circuit pullup
    [BAT_condition.sch, CPU.sch, MAF_input.sch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]
2011-01-22 Fixed small pad in the 40pin signal connector
    [puma.brd]
2011-01-22 Added reset delay, R/C values still to be tested
    [BAT_condition.sch, CPU.sch, MAF_input.sch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]
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2011-01-29 Fixed capacitor vendor number
    [BAT_condition.sch, CPU.sch, MAF_input.sch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]
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2011-02-13 Fresh clone from February 02, 2011 version of nitrousnrg/puma with check in notes Added MCU 3D model
    [connector_board_template.brd, fet test.sch, inductor_test_jig.sch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]
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2011-02-14 broke up 5v_digi net to allow better gnd plane currents
    [BAT_condition.sch, CPU.sch, MAF_input.sch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]
2011-02-14 puma.sch is back to what it was with the linear regulators. We'll make the smaller changes and deal with the regulator upgrade later.
    [puma.sch]
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2011-02-16 updating bom, lets commit this before I run a script to update the footprints for the resistors
    [BAT_condition.sch, CPU.sch, MAF_input.sch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]
2011-02-16 Schematic BOM is now fully populated with only 3 exceptions, .cmp file is obsolete at this point, so it has been removed.
    [BAT_condition.sch, CPU.sch, MAF_input.sch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]
2011-02-17 changed .mod references to relative, vs absolute. Changed fuse to same as used in DFH, basically it's the weak link, that can be replaced with a fuse if required.
    [puma.brd]
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2011-02-20 While I was at it, I created other model MAP bodies we might want.
    [UNIBODY_SMALL-SMT.SLDPRT, UNIBODY_SMALL-SMT.STEP, UNIBODY_SMALL-SMT.STL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]
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2011-02-22 updated MAP module, 3rd vs 1st angle projection issue
    [UNIBODY_CELL.SLDDRW, UNIBODY_CELL.SLDPRT, UNIBODY_CELL.STEP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]
2011-02-23 Silkscreen rearrange, fat 12v track ready to be removed, VR resistors changed to 1210, intra-protection circuits removed, changed XOR resistor to 330ohm, new config for FT232, fixed osc schematic, fi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
    [BAT_condition.sch, CPU.sch, MAF_input.sch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]
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2011-02-23 Removed fuses. Also, I felt like living in a planet that is travelling very quietly across the Universe
    [BAT_condition.sch, CPU.sch, MAF_input.sch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]
2011-02-24 Fixed P&H footprints
    [BAT_condition.sch, CPU.sch, MAF_input.sch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]
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2011-03-13 Incorpored jharveys modules, images, and usb stuff. Added itemos to the TODO about the FT232
    [10103594.SLDASM, 10103594.SLDDRW, 10103594.STEP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]
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2011-03-14 Added reset monitor
    [BAT_condition.sch, CPU.sch, MAF_input.sch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]
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2011-03-16 Added pnp pullup to skip SM during boot. Unsure if the base goes to 5v or 5v_switched
    [BAT_condition.sch, CPU.sch, MAF_input.sch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]
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2011-03-19 Created CAD file for the case, fixed C21
    [BAT_condition.sch, CPU.sch, MAF_input.sch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]
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2011-03-22 Replaced 1/2W resistors by a couple of 1/4W (RPM circuitry)
    [BAT_condition.sch, CPU.sch, MAF_input.sch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]
2011-03-23 Removed reset controller, added simple pullup with cap. Did some board layout too
    [BAT_condition.sch, CPU.sch, MAF_input.sch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]
2011-03-24 Finally,a correct USB setup!
    [BAT_condition.sch, CPU.sch, MAF_input.sch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]
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2011-03-27 minor corrections
    [BAT_condition.sch, CPU.sch, MAF_input.sch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]
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2011-03-27 Schematic correction: 74LS86 to 74HC86
    [BAT_condition.sch, CPU.sch, MAF_input.sch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]
2011-03-29 BOM correction
    [order_BOM.xls]
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2011-04-05 BRV source corrected, now available in the 40 pin header
    [BAT_condition.sch, CPU.sch, MAF_input.sch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]
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2011-06-08 SMPS tests mostly performed, added extra LC filtering to it. Also, added fields for component replacement in case of non availability
    [BAT_condition.sch, CPU.sch, MAF_input.sch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]
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
